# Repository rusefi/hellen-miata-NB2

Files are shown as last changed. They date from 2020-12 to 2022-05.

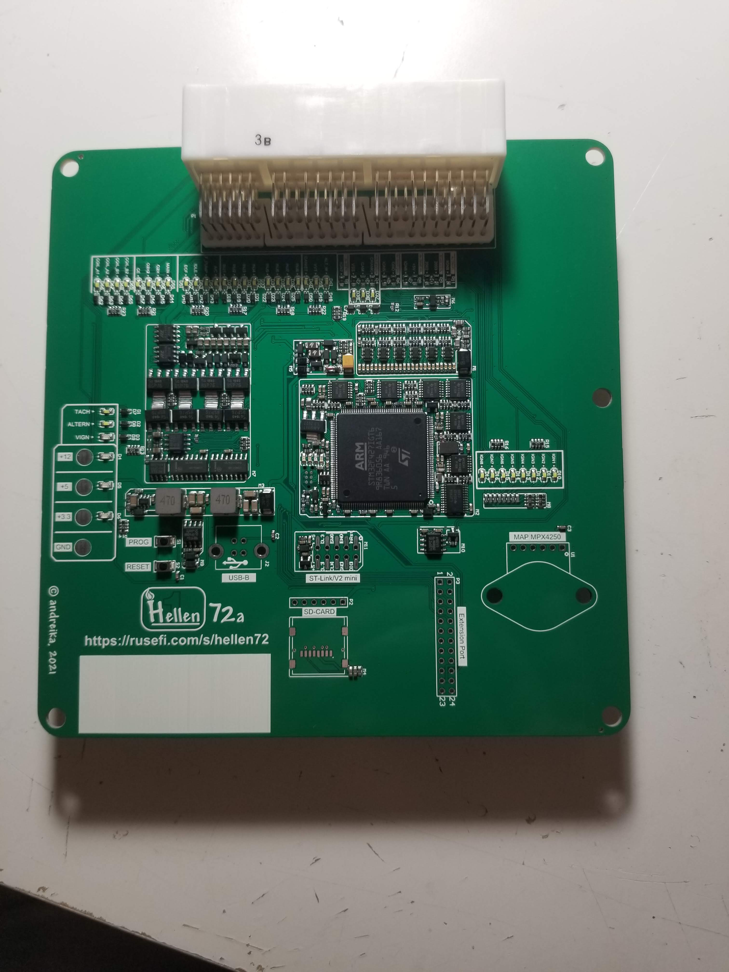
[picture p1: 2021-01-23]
hellen72a.jpg

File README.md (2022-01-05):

# Miata NB2

a rusEFI board with a 72 pin connector. Works for a Mazda Miata NB2 or any generic 8 cylinder vehicle :)

[User Documentation](https://github.com/rusefi/rusefi/wiki/Hellen-NB2)

[Issue Tracker](https://github.com/rusefi/hellen-NB2-issues)

We love https://github.com/thesourcerer8/altium2kicad

https://github.com/rusefi/rusefi/wiki/Mazda-Miata-2001

https://github.com/rusefi/rusefi/wiki/Mazda-Miata-2003

For photos see https://github.com/rusefi/rusefi/wiki/Hellen-NB2

# Compatible cases

89661-3T270

# Hardware

M4 x 10mm will be good for NB external case and internal board to case for both NA and NB.

Powered by https://github.com/andreika-git/hellen-one

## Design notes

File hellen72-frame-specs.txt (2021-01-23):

*** Hellen One: Hellen72 Frame specs (DRAFT) ***

General info: https://rusefi.com/s/hellen72/

EDA Software: Altium Designer

Board/connector footprints source: <.../hw_72_nb>

Pinout spreadsheet: <...>

Modules:
  - mcu/0.1
  - input/0.1
  - output/0.1
  - power5/0.1
  - power12/0.1
  - can/0.1
  - lin/0.1
  - ign8/0.1
  - sd/0.1
  - stlink/0.1
  - knock/0.1

- Additional components:
  - USB-B vertical TH: TE 5787834-1
  - "PROG" button
  - "RESET" button
  - Accelerometer
  - MAP sensor: MPX4250AP
  - SD-Card module connector: <SD-CARD module info>
  - "Extension port" connector: 
    - UART
    - SPI
    - IO1-IO4
    - +3.3V, +5V, +12V, GND

- Board configuration:
  - Jumper resistors for pins:
    - 3L = IN_AFR or OUT_IGN7
    - 3Z = GNDA or OUT_IGN5
    - 4K = V5A or OUT_IGN6
    - 4U = IN_MAP2 or OUT_IGN8
    - IN_VIGN = 4S or 4T
  - Standard input pullups (V5A): 
    - RES1, RES2
    - AUX1, AUX2, AUX3, AUX4
    - TPS, PPS, O2S, O2S2, IAT, CLT
    - CRANK, CAM, VSS
    - SENS3 (FUEL_LEVEL)
  - Standard input pulldowns (GNDA): 
    - MAP1, MAP2, MAP3, MAP4
    - KNOCK
    - SENS1, SENS2, SENS4
  - Additional pulldowns (GNDA):
    - IN_MAF (1k)

- Additional LEDS:
  - IGN1-IGN8 (to GND)
  - INJ1-INJ8 (to +12V, protected)
  - AC, PUMP, IDLE, ECF, VVT, O2H, O2H2, CE, ALT_WARN, MAIN, CANIST (to +12V, protected)
  - TACH, ALTERN, VIGN (to GND, protected)
  - CRANK, CAM, VSS (to +5V, protected)
  - +5V, +3.3V
  - Jumper resistors for LEDS: VSS, CAM, CRANK

- Additional TEST PADS:
  - +12V
  - +5V
  - +3.3V
  - GND

- Silkscreen:
  - silkscreen/board orientation - the ECU connector is at the top
  - all pins named (both sides)
  - https://rusefi.com/s/hellen72/
  - "for notes" area 50x20 mm

- Special layout requirements:
  - SD-Card should be 10-20 mm away from other components
  - MPX4250 hose output opposite to the ECU connector

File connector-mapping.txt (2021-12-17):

(1-30)  1C 1F    1L 1O 1R 1U 1X    2C 2F 2I    2O 2R    3C 3F 3I 3L 3O    3T 3W 3Z    4C 4F 4I 4K 4N    4T 4W    4AB 4AE 4AH
         1  2     3  4  5  6  7     8  9 10    11 12    13 14 15 16 17    18 19 20    21 22 23 24 25    26 27     28  29  30

(31-65) 1B 1E 1H 1K 1N 1Q 1T 1W    2B 2E 2H 2K 2N 2Q    3B 3E 3H 3K 3N 3Q 3S 3V 3Y    4B 4E 4H 4J 4M 4P 4S 4V 4X 4AA 4AD 4AG 
        31 32 33 34 35 36 37 38    39 40 41 42 43 44    45 46 47 48 49 50 51 52 53    54 55 56 57 58 59 60 61 62  63  64  65

(66-94) 1A 1D 1G 1J 1M    1S 1V    2A 2D 2G 2J 2M 2P    3A 3D    3J 3M 3P    3U 3X    4A 4D       4L 4O 4R 4U     4Z 4AC 4AF
        66 67 68 69 70    71 72    73 74 75 76 77 78    79 80    81 82 83    84 85    86 87       88 89 90 91     92  93  94

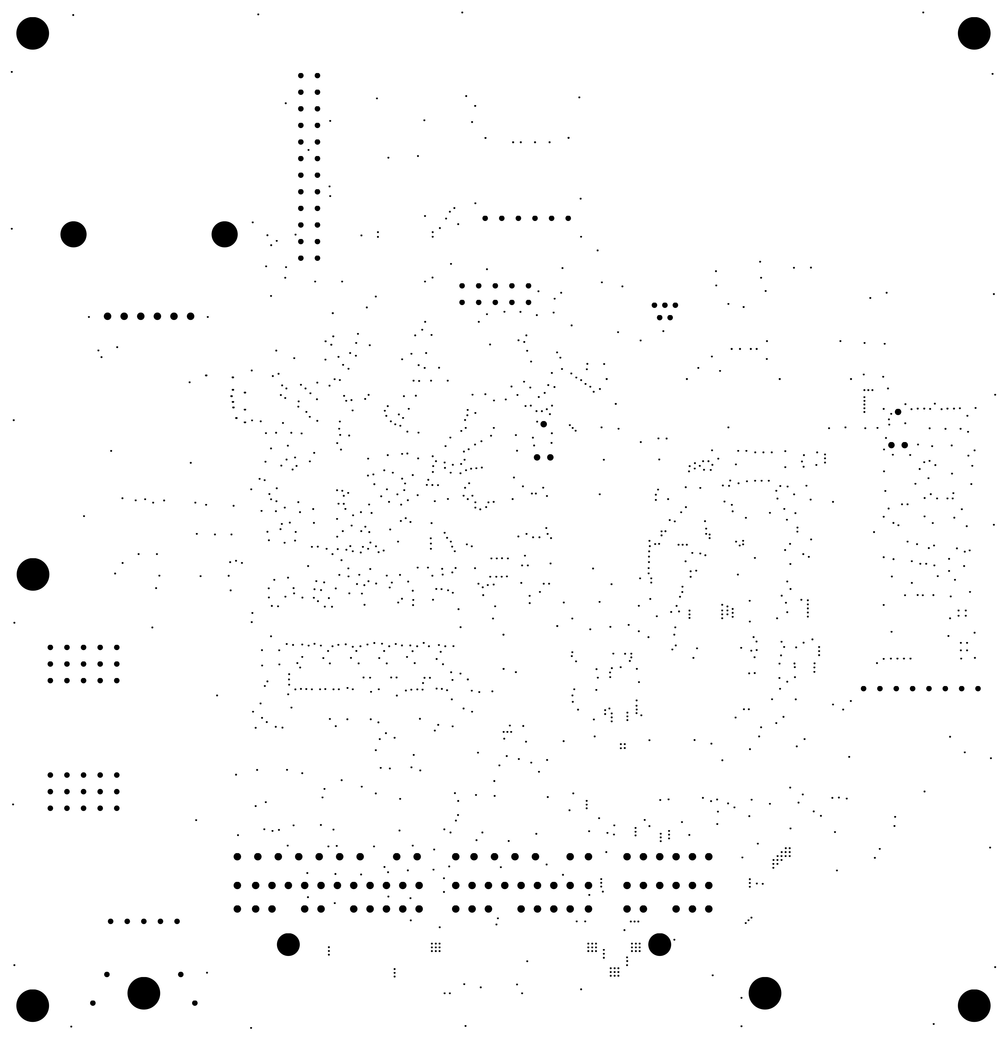
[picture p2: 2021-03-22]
boards/hellen72-c/board/misc/hellen72-c-outline.png

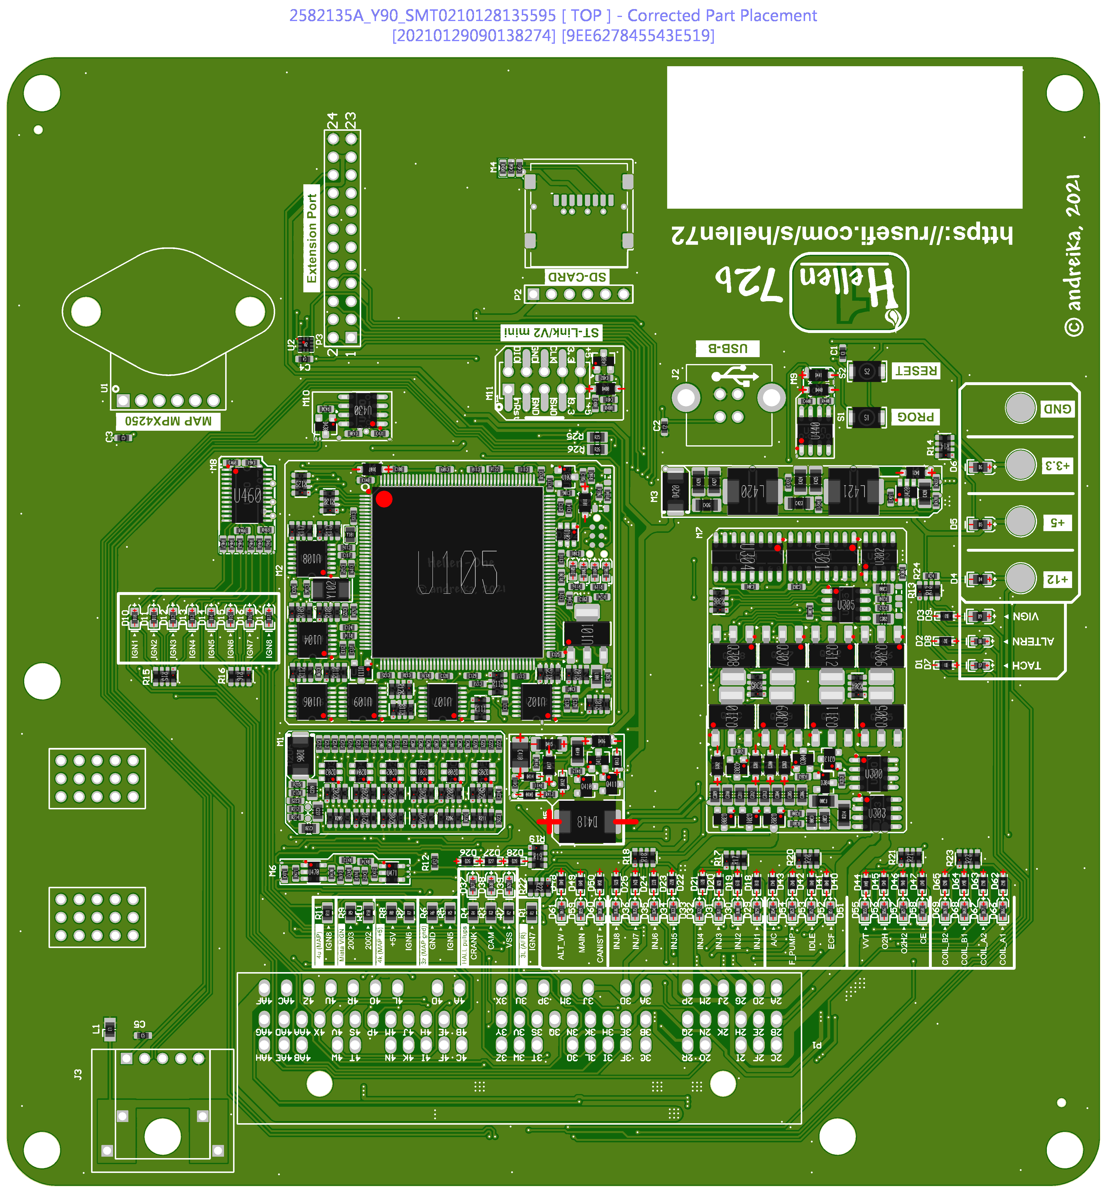
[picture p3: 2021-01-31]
boards/hellen72b/board/Produce_DanZhi.SMT_Snapshot.Top.2582135A_Y90.SMT0210128135595.png

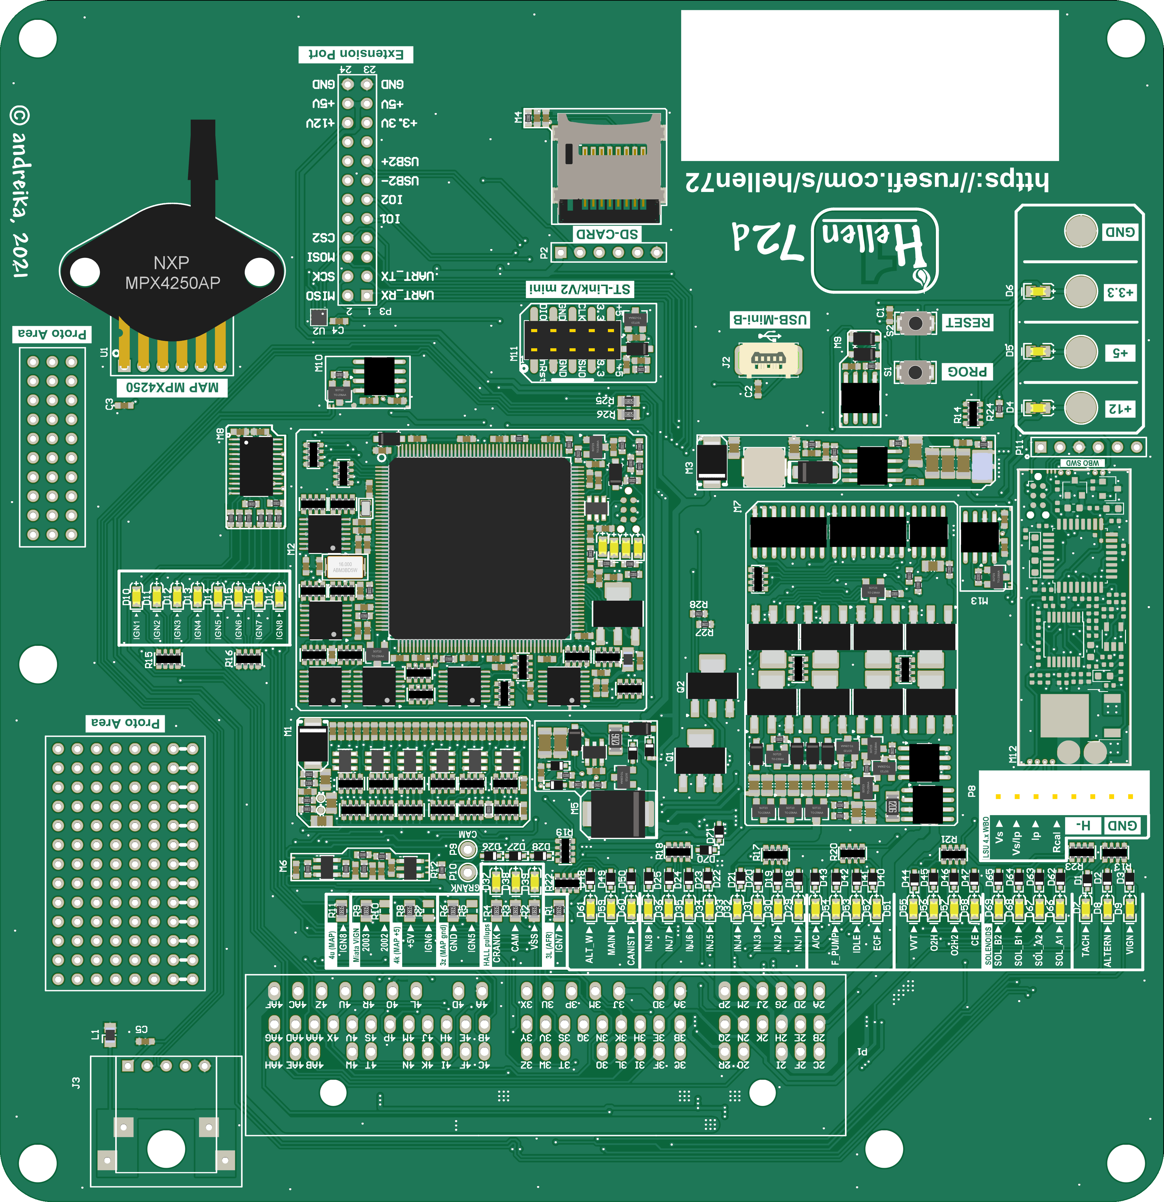
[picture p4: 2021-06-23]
boards/hellen72-d/board/hellen72-d.png

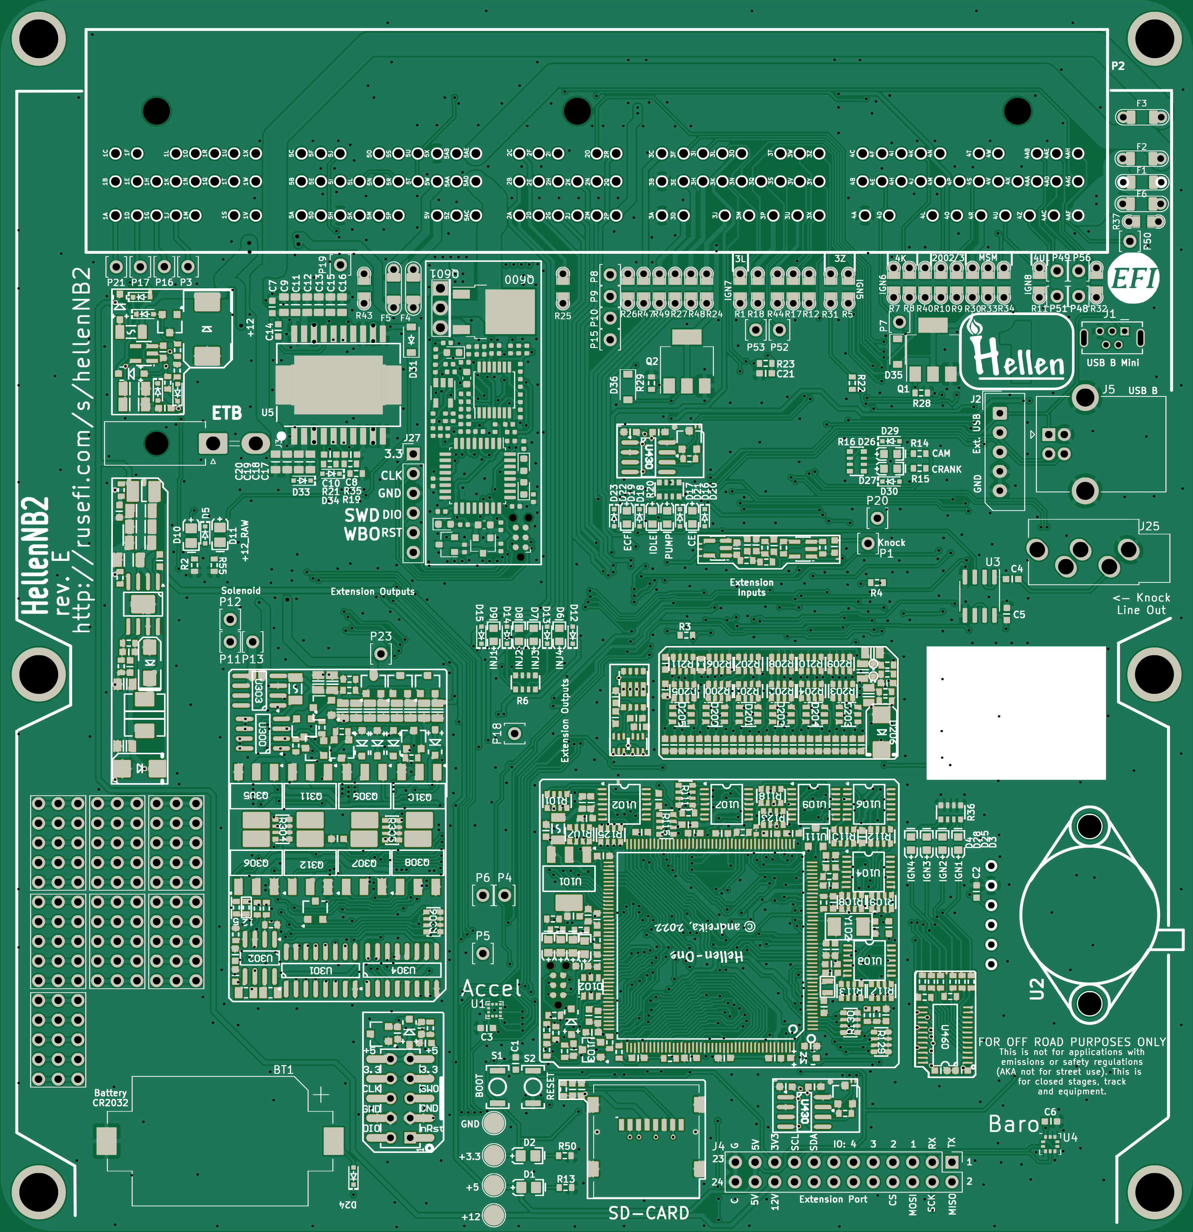
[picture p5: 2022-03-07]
boards/hellen72_NB2-e/board/misc/hellen72_NB2-e-top.png

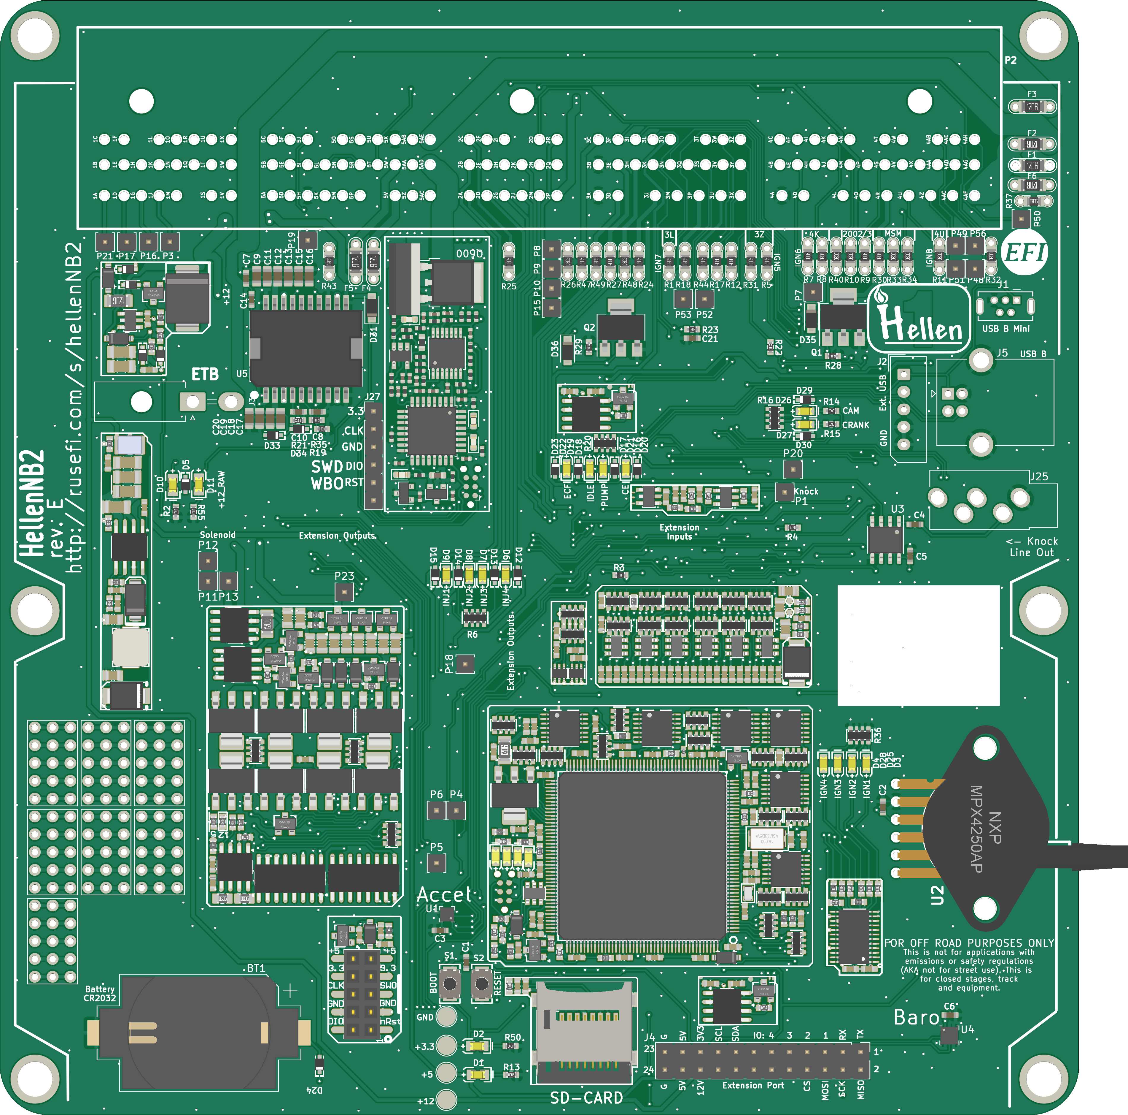
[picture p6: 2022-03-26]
boards/hellen72_NB2-e/board/hellen72_NB2-e.png

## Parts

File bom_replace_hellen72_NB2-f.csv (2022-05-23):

# remove the jumper connection from VCC_PP1 to +5V: we need +12v power supply for push-pull outputs.
R309
# remove +5V pull-ups from SPI1 | because we use it with +3.3v accelerometer
R103
R105
# remove jumper resistor connecting BOOT1 with A22 input line | because we use STM32F4
R131
# STM32
U105 | STM32F407IGT6 | LQFP176 | C33993
# DC-DC Inductor
L421 | MWSA0503S-100MT | SMD-5.2x5.4x2.8 | C408412
L420 | LBC3225T2R2MR | 1210 | C223413
# LMR14020->LMR14030 (more power | no problem)
U420 | LMR14030 | SOP8 | C182078
#fuses
F410 | nSMD050-24V | F1206 | C70076
F300 | nSMD050-24V | F1206 | C70076
F1 | Fuse-5A-1206 | F1206 | C553924
F2 | Fuse-5A-1206 | F1206 | C553924
F3 | Fuse-5A-1206 | F1206 | C553924
F4 | Fuse-5A-1206 | F1206 | C553924
F5 | Fuse-5A-1206 | F1206 | C553924
F6 | Fuse-5A-1206 | F1206 | C553924
#INJ low-side
Q305 | ZXMS6005SGTA | SOT-223 | C174042
Q306 | ZXMS6005SGTA | SOT-223 | C174042
Q307 | ZXMS6005SGTA | SOT-223 | C174042
Q308 | ZXMS6005SGTA | SOT-223 | C174042
Q309 | ZXMS6005SGTA | SOT-223 | C174042
Q310 | ZXMS6005SGTA | SOT-223 | C174042
Q311 | ZXMS6005SGTA | SOT-223 | C174042
Q312 | ZXMS6005SGTA | SOT-223 | C174042
#power distribution
U103 | AP2331W-7 | SOT-23 | C460346
U480 | AP2331W-7 | SOT-23 | C460346
##### 2022-03-08 JLC stock replacements:
#green LED 0805
D1 | LED-GREEN-0805 | C434432
D2 | LED-GREEN-0805 | C434432
D10 | LED-GREEN-0805 | C434432
D11 | LED-GREEN-0805 | C434432
#wbo opamp
U601 | GS8551-TR | TSOT23-5 | C157715
#wbo low-side
Q600 | VND14NV04TR-E | DPAK | C2649436
Q600_2 | VND14NV04TR-E | DPAK | C2649436
#capacitor 10uF 25V 0603
C300 | 10u | C0603 | C2922482
# ignition buffer
U460 | 74LVC4245APW | TSSOP24 | C6091
# trigger schmidt buffer
U490 | SN74LVC2G17DCKR | SOT-363 | C50714
U491 | SN74LVC2G17DCKR | SOT-363 | C50714
#p-channel mosfets
Q300 | WST4045 | SOT-23 | C719073
Q301 | WST4045 | SOT-23 | C719073
Q302 | WST4045 | SOT-23 | C719073
Q303 | WST4045 | SOT-23 | C719073
Q304 | WST4045 | SOT-23 | C719073
Q313 | WST4045 | SOT-23 | C719073
Q314 | WST4045 | SOT-23 | C719073
#pressure sensor
U4 | LPS22HBTR | HLGA-10 | C94049
#non-JLC componentts
#WBO low-side
Q601
Q601_2
#WBO STM32
U602
U602_2
#include board_id_72_NB2-f.csv

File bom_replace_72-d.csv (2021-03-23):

# remove the jumper connection from VCC_PP1 to +5V: we need +12v power supply for push-pull outputs.
R309
# remove +5V pull-ups from SPI1 | because we use it with +3.3v accelerometer
R103
R105
# remove jumper resistor connecting BOOT1 with A22 input line | because we use STM32F4
R131
# JLC stock adjustments
U103 | AP2331TDSA-7 | SOT-23 | C183303
U480 | AP2331TDSA-7 | SOT-23 | C183303
U600 | LMV324IPWR | TSSOP14 | C398929

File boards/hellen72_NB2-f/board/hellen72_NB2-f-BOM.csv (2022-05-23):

Comment | Designator | Footprint | LCSC Part #
BATTERY_CR2032 | BT1 | BATTERY-2032 | C70377
100n | C1, C2, C3, C5, C6, C7, C204, C205, C206, C207, C212, C213, C214, C215, C220, C221, C222, C223, C224, C225, C226, C460, C461, C101, C105, C106, C107, C108, C109, C110, C111, C112, C113, C117, C118, C119, C120, C121, C122, C123, C124, C125, C126, C127, C128, C129, C130, C135, C139, C480, C481, C482, C430, C431, C470, C411, C413, C420, C430_2, C431_2 | C0603 | C14663
10u | C4 | C0603 | C19702
6.8n | C8 | C0603 | C1631
10u | C9, C11, C12, C13, C15, C16, C17, C18, C19, C20, C304, C305, C306, C307, C308, C309, C310, C311, C312, C313, C425, C426 | C0805 | C15850
10n | C10, C201, C208, C209, C210, C211, C301, C302, C428 | C0603 | C57112
220n | C14 | C0603 | C21120
100n | C21 | C0603
LED-BLUE-0603 | D3, D4, D25, D28, D105, D602 | LED-0603 | C72041
1N4148WS | D5, D12, D13, D14, D15, D20, D21, D22, D23, D24, D29, D30, D33, D34, D410, D412, D413, D414 | SOD-323 | C2128
LED-RED-0603 | D6, D7, D8, D9, D103, D600, D603 | LED-0603 | C2286
LED-WHITE-0603 | D16, D17, D18, D19, D26, D27 | LED-0603 | C2290
B5819W | D31, D35, D36, D101, D107, D300, D301, D302, D303, D480, D416, D417 | SOD-123 | C8598
LOGO | G1 | LOGO
DISCLAIMER | G2 | Off_Road_Disclaimer
LOGO | G3 | LOGO
PROTO_AREA | G4 | PROTO_AREA
PROTO_AREA | G5 | PROTO_AREA
PROTO_AREA | G6 | PROTO_AREA
PROTO_AREA | G7 | PROTO_AREA
PROTO_AREA | G9 | PROTO_AREA
PROTO_AREA | G11 | PROTO_AREA
PROTO_AREA | G12 | PROTO_AREA
USB_B_Mini | J1 | USB-MINI-B-VERTICAL | C13453
Conn_01x05_Male | J2 | Molex_SPOX_5267-05A_1x05_P2.50mm_Vertical
MiniFit | J3 | Molex-39301020 | C240832
Conn_02x12_Odd_Even | J4 | PinHeader_2x12_P2.54mm_Vertical
USB_B | J5 | USB_B | C46392
Conn_01x01 | J11 | MountingHole_4.5mm_Pad
Conn_01x01 | J13 | MountingHole_4.5mm_Pad
Conn_01x01 | J14 | MountingHole_4.5mm_Pad
Conn_01x01 | J15 | MountingHole_4.5mm_Pad
Conn_01x01 | J16 | MountingHole_4.5mm_Pad
Conn_01x01 | J17 | MountingHole_4.5mm_Pad
Conn_01x01 | J19 | TestPoint_Pad_D2.0mm
Conn_01x01 | J20 | TestPoint_Pad_D2.0mm
Conn_01x01 | J21 | TestPoint_Pad_D2.0mm
Conn_01x01 | J22 | TestPoint_Pad_D2.0mm
Conn_01x01 | J24 | TestPoint_Pad_D2.0mm
AudioJack3_SwitchTR | J25 | Jack_3.5mm_PJ-3250-5A | C165947
Conn_01x06 | J27 | PinHeader_1x06_P2.54mm_Vertical
Pad | P1 | PAD-TH
8-5353015-1 | P2 | 8-5353015-1
Pad | P3 | PAD-TH
Pad | P4 | PAD-TH
Pad | P5 | PAD-TH
Pad | P6 | PAD-TH
Pad | P7 | PAD-TH
Pad | P8 | PAD-TH
Pad | P9 | PAD-TH
Pad | P10 | PAD-TH
Pad | P11 | PAD-TH
Pad | P12 | PAD-TH
Pad | P13 | PAD-TH
Pad | P15 | PAD-TH
Pad | P16 | PAD-TH
Pad | P17 | PAD-TH
Pad | P18 | PAD-TH
Pad | P19 | PAD-TH
Pad | P20 | PAD-TH
Pad | P21 | PAD-TH
Pad | P23 | PAD-TH
Pad | P48 | PAD-TH
Pad | P49 | PAD-TH
Pad | P50 | PAD-TH
Pad | P51 | PAD-TH
Pad | P52 | PAD-TH
Pad | P53 | PAD-TH
Pad | P56 | PAD-TH
AUIPS2041LTR | Q1, Q2 | SOT-223 | C113610
Jumper-Pad-Pad | R1 | PAD-0805-PAD
5.1k | R2, R55, R132 | R0603 | C23186
4.7k | R3, R302, R303, R313 | R0603 | C23162
1k | R4, R311, R314 | R0603 | C21190
Jumper-Pad-Pad | R5 | PAD-0805-PAD
4.7k | R6, R16, R200, R201, R202, R203, R204, R205, R207 | R0603-4 | C1980
Jumper-Pad-Pad | R7 | PAD-0805-PAD
Jumper-Pad-Pad | R8, R9, R12, R17, R18, R24, R25, R26, R27, R30, R31, R32, R34, R38, R39, R40, R43, R44, R47, R48, R49 | PAD-0805-PAD | C17477
Jumper-Pad-Pad | R10 | PAD-0805-PAD
Jumper-Pad-Pad | R11 | PAD-0805-PAD
1.6k | R13 | R0603 | C22847
0 | R14, R15, R23, R310 | R0603 | C21189
10k | R19, R28, R29, R102, R121, R127, R128, R300, R301, R307, R308, R315, R480, R421, R134 | R0603 | C25804
20k | R20 | R0603-4 | C12004
100 | R21, R104, R106 | R0603 | C22775
680k | R22 | R0603 | C25822
Jumper-Pad-Pad | R33 | PAD-0805-PAD
100k | R35, R471, R473 | R0603 | C25803
470 | R36 | R0603-4 | C25510
Jumper-Pad-Pad | R37 | PAD-0805-PAD
750 | R50 | R0603 | C23241
Button_SPST | S1, S2 | SMD-2_2.9x3.9x1.7 | C115357
LIS2DW12TR | U1 | LGA-12_2x2mm_P0.5mm | C189624
MPX4_MAP | U2 | MPX-4_MAP
MCP6002-xSN | U3 | SO8 | C7377
L6205PD | U5 | SO20POWER | C36543
1n | C200, C202, C203, C216, C217, C218, C219, C490, C491, C492, C493 | C0603 | C1588
2.2u | C227, C228, C229 | C0805 | C49217
SRV05-4-P-T7 | D200, D201, D202, D203, D204, D205, D102 | SOT23-6 | C85364
P6SMB6.8CA | D206, D421 | SMB | C78395
680k | R206, R209, R211, R490 | R0603-4 | C145776
10k | R208, R210, R129, R130, R304, R305, R306, R491 | R0603-4 | C29718
510 | R212, R213, R214, R215, R116, R119, R120, R124, R133 | R0603 | C23193
3.3k | R216 | R0603 | C22978
10 | R461, R462, R463, R464, R466, R467, R468, R469 | R0603 | C22859
4.7u | C102, C103, C104, C137, C138, C140, C427, C616 | C0603 | C19666
2.2u | C114, C131 | C0603 | C23630
12p | C115, C116 | C0603 | C38523
18p | C132, C136 | C0603 | C1647
1u | C133 | C0603 | C15849
LED-GREEN-0603 | D104, D601 | LED-0603 | C72043
LED-YELLOW-0603 | D106 | LED-0603 | C72038
SMD1206B035TF/16 | F101 | SMD1206 | C269114
4.7k | R101, R107, R108, R109, R110, R111, R112, R113, R115, R117, R118, R125, R126 | R0603-4 | C66697
47 | R114 | R0603 | C23182
2.2k | R122, R123 | R0603 | C4190
AMS1117-3.3 | U101 | SOT-223 | C6186
MCP6004 | U102, U104, U106, U107, U108, U109, U600 | TSSOP14 | C50282
XC6206P332MR | U111, U604 | SOT-23 | C5446
32.768 kHz | Y101 | SMD2012 | C99009
20 MHz | Y102 | SMD5032 | C112566
22u | C450, C451 | C0603 | C59461
Molex MicroSD 47219-2001 | J450 | SDAMB-012 | C164170
33k | R450, R474, R411 | R0603 | C4216
PSM712-LF | D304, D305, D411 | SOT-23 | C32677
100 | R312, R316 | R0805 | C17408
RZ7899 | U300, U303 | SO8 | C92373
ULN2003AD | U301, U304 | SOIC16 | C7512
TC4427 | U302 | SO8 | C20551
ST/Link 2x5 | P480 | HDR2x5-F-TH-SMD
PESD1CAN | D430, D430_2 | SOT-23 | C343993
120 | R430, R430_2 | R0603 | C22787
TJA1051T/3/1J | U430, U430_2 | SO8 | C38695
3.3n | C471 | C0603 | C1613
330p | C472 | C0603 | C1664
47p | C473 | C0603 | C1671
680p | C474 | C0603 | C1630
470k | R470 | R0603 | C23178
12k | R472, R423 | R0603 | C22790
LMV321IDBVR | U470, U471 | SOT23-5 | C7972
47u | C410, C412 | C1206 | C96123
SMCJ30A | D418 | SMC | C310046
6.8k | R410, R413 | R0603 | C23212
MIC5205-3.3YM5 | U410 | SOT23-5 | C37970
10u | C421, C422, C423, C424 | C1206 | C13585
220p | C429 | C0603 | C1603
SS34 | D420 | SMA | C8678
1 | R420 | R0603 | C22936
68k | R422 | R0603 | C23231
1u | C600, C607, C609, C610, C611 | C0402 | C52923
100n | C601, C602, C605, C608, C612, C613, C614, C615 | C0402 | C1525
33n | C603 | C0402 | C1585
DNP | C604 | C0402
DNP | C606 | C0402
1k | R600, R601, R616, R617, R622, R626, R627, R628 | R0402 | C11702
68k | R602, R603 | R0402 | C36871
10k | R604, R605, R613, R614, R618, R619, R625 | R0402 | C25744
10 | R606 | R0402 | C25077
22k | R607 | R0402 | C25768
47 | R608 | R0402 | C25118
61.9 | R609 | R0603 | C23092
20k | R610, R611, R612 | R0402 | C25765
100k | R615, R621 | R0402 | C25741
27k | R620, R623 | R0402 | C25771
3.3k | R624 | R0402 | C25890
REF3033 | U603 | SOT-23 | C36658
STM32F407IGT6 | U105 | LQFP176 | C33993
MWSA0503S-100MT | L421 | SMD-5.2x5.4x2.8 | C408412
LBC3225T2R2MR | L420 | 1210 | C223413
LMR14030 | U420 | SOP8 | C182078
nSMD050-24V | F410, F300 | F1206 | C70076
Fuse-5A-1206 | F1, F2, F3, F4, F5, F6 | F1206 | C553924
ZXMS6005SGTA | Q305, Q306, Q307, Q308, Q309, Q310, Q311, Q312 | SOT-223 | C174042
AP2331W-7 | U103, U480 | SOT-23 | C460346
GS8551-TR | U601 | TSOT23-5 | C157715
VND14NV04TR-E | Q600, Q600_2 | DPAK | C2649436
10u | C300 | C0603 | C2922482
74LVC4245APW | U460 | TSSOP24 | C6091
SN74LVC2G17DCKR | U490, U491 | SOT-363 | C50714
WST4045 | Q300, Q301, Q302, Q303, Q304, Q313, Q314 | SOT-23 | C719073
LPS22HBTR | U4 | HLGA-10 | C94049

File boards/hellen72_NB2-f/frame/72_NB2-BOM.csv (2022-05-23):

Comment | Designator | Footprint | LCSC Part #
BATTERY_CR2032 | BT1 | BATTERY-2032 | C70377
100n | C1 | C0603 | C14663
100n | C2 | C0603 | C14663
100n | C3 | C0603 | C14663
10u | C4 | C0603 | C19702
100n | C5 | C0603 | C14663
100n | C6 | C0603 | C14663
100n | C7 | C0603 | C14663
6.8n | C8 | C0603 | C1631
10u | C9 | C0805 | C15850
10n | C10 | C0603 | C57112
10u | C11 | C0805 | C15850
10u | C12 | C0805 | C15850
10u | C13 | C0805 | C15850
220n | C14 | C0603 | C21120
10u | C15 | C0805 | C15850
10u | C16 | C0805 | C15850
10u | C17 | C0805 | C15850
10u | C18 | C0805 | C15850
10u | C19 | C0805 | C15850
10u | C20 | C0805 | C15850
100n | C21 | C0603
LED-GREEN-0805 | D1 | LED-0805 | C2297
LED-GREEN-0805 | D2 | LED-0805 | C2297
LED-BLUE-0603 | D3 | LED-0603 | C72041
LED-BLUE-0603 | D4 | LED-0603 | C72041
1N4148WS | D5 | SOD-323 | C2128
LED-RED-0603 | D6 | LED-0603 | C2286
LED-RED-0603 | D7 | LED-0603 | C2286
LED-RED-0603 | D8 | LED-0603 | C2286
LED-RED-0603 | D9 | LED-0603 | C2286
LED-GREEN-0805 | D10 | LED-0805 | C2297
LED-GREEN-0805 | D11 | LED-0805 | C2297
1N4148WS | D12 | SOD-323 | C2128
1N4148WS | D13 | SOD-323 | C2128
1N4148WS | D14 | SOD-323 | C2128
1N4148WS | D15 | SOD-323 | C2128
LED-WHITE-0603 | D16 | LED-0603 | C2290
LED-WHITE-0603 | D17 | LED-0603 | C2290
LED-WHITE-0603 | D18 | LED-0603 | C2290
LED-WHITE-0603 | D19 | LED-0603 | C2290
1N4148WS | D20 | SOD-323 | C2128
1N4148WS | D21 | SOD-323 | C2128
1N4148WS | D22 | SOD-323 | C2128
1N4148WS | D23 | SOD-323 | C2128
1N4148WS | D24 | SOD-323 | C2128
LED-BLUE-0603 | D25 | LED-0603 | C72041
LED-WHITE-0603 | D26 | LED-0603 | C2290
LED-WHITE-0603 | D27 | LED-0603 | C2290
LED-BLUE-0603 | D28 | LED-0603 | C72041
1N4148WS | D29 | SOD-323 | C2128
1N4148WS | D30 | SOD-323 | C2128
B5819W | D31 | SOD-123 | C8598
1N4148WS | D33 | SOD-323 | C2128
1N4148WS | D34 | SOD-323 | C2128
B5819W | D35 | SOD-123 | C8598
B5819W | D36 | SOD-123 | C8598
Fuse-Pad-Pad | F1 | PAD-1206-PAD | C182446
Fuse-Pad-Pad | F2 | PAD-1206-PAD | C182446
Fuse-Pad-Pad | F3 | PAD-1206-PAD | C182446
Fuse-Pad-Pad | F4 | PAD-1206-PAD | C182446
Fuse-Pad-Pad | F5 | PAD-1206-PAD | C182446
Fuse-Pad-Pad | F6 | PAD-1206-PAD | C182446
LOGO | G1 | LOGO
DISCLAIMER | G2 | Off_Road_Disclaimer
LOGO | G3 | LOGO
PROTO_AREA | G4 | PROTO_AREA
PROTO_AREA | G5 | PROTO_AREA
PROTO_AREA | G6 | PROTO_AREA
PROTO_AREA | G7 | PROTO_AREA
PROTO_AREA | G9 | PROTO_AREA
PROTO_AREA | G11 | PROTO_AREA
PROTO_AREA | G12 | PROTO_AREA
USB_B_Mini | J1 | USB-MINI-B-VERTICAL | C13453
Conn_01x05_Male | J2 | Molex_SPOX_5267-05A_1x05_P2.50mm_Vertical
MiniFit | J3 | Molex-39301020 | C240832
Conn_02x12_Odd_Even | J4 | PinHeader_2x12_P2.54mm_Vertical
USB_B | J5 | USB_B | C46392
Conn_01x01 | J11 | MountingHole_4.5mm_Pad
Conn_01x01 | J13 | MountingHole_4.5mm_Pad
Conn_01x01 | J14 | MountingHole_4.5mm_Pad
Conn_01x01 | J15 | MountingHole_4.5mm_Pad
Conn_01x01 | J16 | MountingHole_4.5mm_Pad
Conn_01x01 | J17 | MountingHole_4.5mm_Pad
Conn_01x01 | J19 | TestPoint_Pad_D2.0mm
Conn_01x01 | J20 | TestPoint_Pad_D2.0mm
Conn_01x01 | J21 | TestPoint_Pad_D2.0mm
Conn_01x01 | J22 | TestPoint_Pad_D2.0mm
Conn_01x01 | J24 | TestPoint_Pad_D2.0mm
AudioJack3_SwitchTR | J25 | Jack_3.5mm_PJ-3250-5A | C165947
Conn_01x06 | J27 | PinHeader_1x06_P2.54mm_Vertical
Module:input/0.1 | M1 | input
Module:ign8/0.2 | M2 | ign8
Module:mcu/0.6 | M3 | mcu
Module:sd/0.1 | M4 | sd
Module:output/0.3 | M5 | output
Module:dinput4/0.1 | M6 | dinput4
Module:stlink/0.1 | M7 | stlink
Module:can/0.1 | M8 | can
Module:knock/0.1 | M9 | knock
Module:power12/0.2 | M10 | power12
Module:power5/0.2 | M11 | power5
Module:wbo/0.3 | M12 | wbo
Module:can/0.1 | M13 | can
Pad | P1 | PAD-TH
8-5353015-1 | P2 | 8-5353015-1
Pad | P3 | PAD-TH
Pad | P4 | PAD-TH
Pad | P5 | PAD-TH
Pad | P6 | PAD-TH
Pad | P7 | PAD-TH
Pad | P8 | PAD-TH
Pad | P9 | PAD-TH
Pad | P10 | PAD-TH
Pad | P11 | PAD-TH
Pad | P12 | PAD-TH
Pad | P13 | PAD-TH
Pad | P15 | PAD-TH
Pad | P16 | PAD-TH
Pad | P17 | PAD-TH
Pad | P18 | PAD-TH
Pad | P19 | PAD-TH
Pad | P20 | PAD-TH
Pad | P21 | PAD-TH
Pad | P23 | PAD-TH
Pad | P48 | PAD-TH
Pad | P49 | PAD-TH
Pad | P50 | PAD-TH
Pad | P51 | PAD-TH
Pad | P52 | PAD-TH
Pad | P53 | PAD-TH
Pad | P56 | PAD-TH
AUIPS2041LTR | Q1 | SOT-223 | C113610
AUIPS2041LTR | Q2 | SOT-223 | C113610
Jumper-Pad-Pad | R1 | PAD-0805-PAD
5.1k | R2 | R0603 | C23186
4.7k | R3 | R0603 | C23162
1k | R4 | R0603 | C21190
Jumper-Pad-Pad | R5 | PAD-0805-PAD
4.7k | R6 | R0603-4 | C1980
Jumper-Pad-Pad | R7 | PAD-0805-PAD
Jumper-Pad-Pad | R8 | PAD-0805-PAD | C17477
Jumper-Pad-Pad | R9 | PAD-0805-PAD | C17477
Jumper-Pad-Pad | R10 | PAD-0805-PAD
Jumper-Pad-Pad | R11 | PAD-0805-PAD
Jumper-Pad-Pad | R12 | PAD-0805-PAD | C17477
1.6k | R13 | R0603 | C22847
0 | R14 | R0603 | C21189
0 | R15 | R0603 | C21189
4.7k | R16 | R0603-4 | C1980
Jumper-Pad-Pad | R17 | PAD-0805-PAD | C17477
Jumper-Pad-Pad | R18 | PAD-0805-PAD | C17477
10k | R19 | R0603 | C25804
20k | R20 | R0603-4 | C12004
100 | R21 | R0603 | C22775
680k | R22 | R0603 | C25822
0 | R23 | R0603 | C21189
Jumper-Pad-Pad | R24 | PAD-0805-PAD | C17477
Jumper-Pad-Pad | R25 | PAD-0805-PAD | C17477
Jumper-Pad-Pad | R26 | PAD-0805-PAD | C17477
Jumper-Pad-Pad | R27 | PAD-0805-PAD | C17477
10k | R28 | R0603 | C25804
10k | R29 | R0603 | C25804
Jumper-Pad-Pad | R30 | PAD-0805-PAD | C17477
Jumper-Pad-Pad | R31 | PAD-0805-PAD | C17477
Jumper-Pad-Pad | R32 | PAD-0805-PAD | C17477
Jumper-Pad-Pad | R33 | PAD-0805-PAD
Jumper-Pad-Pad | R34 | PAD-0805-PAD | C17477
100k | R35 | R0603 | C25803
470 | R36 | R0603-4 | C25510
Jumper-Pad-Pad | R37 | PAD-0805-PAD
Jumper-Pad-Pad | R38 | PAD-0805-PAD | C17477
Jumper-Pad-Pad | R39 | PAD-0805-PAD | C17477
Jumper-Pad-Pad | R40 | PAD-0805-PAD | C17477
Jumper-Pad-Pad | R43 | PAD-0805-PAD | C17477
Jumper-Pad-Pad | R44 | PAD-0805-PAD | C17477
Jumper-Pad-Pad | R47 | PAD-0805-PAD | C17477
Jumper-Pad-Pad | R48 | PAD-0805-PAD | C17477
Jumper-Pad-Pad | R49 | PAD-0805-PAD | C17477
750 | R50 | R0603 | C23241
5.1k | R55 | R0603 | C23186
Button_SPST | S1 | SMD-2_2.9x3.9x1.7 | C115357
Button_SPST | S2 | SMD-2_2.9x3.9x1.7 | C115357
LIS2DW12TR | U1 | LGA-12_2x2mm_P0.5mm | C189624
MPX4_MAP | U2 | MPX-4_MAP
MCP6002-xSN | U3 | SO8 | C7377
LPS25HB | U4 | HLGA-10 | C87898
L6205PD | U5 | SO20POWER | C36543

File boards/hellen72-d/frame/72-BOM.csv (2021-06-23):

Comment | Designator | Footprint | LCSC Part #
100n | C1, C2, C3, C4, C5 | C0603 | C14663
1N4148WS | D1, D2, D3, D18, D19, D20, D21, D22, D23, D24, D25, D26, D27, D28, D40, D41, D42, D43, D44, D45, D46, D47, D48, D49, D50, D62, D63, D64, D65, D70, D71 | SOD-323 | C2128
LED-GREEN-0805 | D4, D5, D6 | LED-0805 | C2297
LED-WHITE-0603 | D7, D8, D51, D52, D53, D54, D55, D56, D57, D58, D59, D60, D61, D66, D67, D68, D69 | LED-0603 | C2290
LED-GREEN-0603 | D9 | LED-0603 | C72043
LED-BLUE-0603 | D10, D11, D12, D13, D14, D15, D16, D17 | LED-0603 | C72041
LED-RED-0603 | D29, D30, D31, D32, D33, D34, D35, D36, D37, D38, D39 | LED-0603 | C2286
USB-Mini-V | J2 | USB-B-VERTICAL | C13453
USB-Adapter | J3 | USB-B-VERTICAL
GZ2012D101TF | L1 | L0805 | C1015
Module:input/0.1 | M1
Module:mcu/0.3 | M2
Module:power5/0.2 | M3
Module:sd/0.1 | M4
Module:power12/0.2 | M5
Module:knock/0.1 | M6
Module:output/0.2 | M7
Module:ign8/0.1 | M8
Module:lin/0.1 | M9
Module:can/0.1 | M10, M13
Module:stlink/0.1 | M11
Module:wbo/0.2 | M12
XH-8A | P8 | CONN-XH-8A | C146110
CAM | P9
CRANK | P10
WBO SWD | P11
AUIPS2041LTR | Q1, Q2 | SOT-223 | C113610
0 | R1, R2, R3, R4, R6, R8, R9, R11, R25, R26 | R0805 | C17477
1k | R12 | R0603 | C21190
10k | R13, R20, R21, R22, R23 | R0603-4 | C29718
1k | R14, R19 | R0603-4 | C20197
470 | R15, R16 | R0603-4 | C25510
4.7k | R17, R18 | R0603-4 | C1980
2.2k | R24 | R0603 | C4190
10k | R27, R28 | R0603 | C25804
Switch SPST | S1, S2 | SMD-2_2.9x3.9x1.7 | C115357
Abs. Pressure Sensor | U1 | 867B
LIS2DW12TR | U2 | LGA12 | C189624

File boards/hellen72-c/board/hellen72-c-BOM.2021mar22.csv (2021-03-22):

Comment | Designator | Footprint | LCSC Part #
100n | C1, C2, C3, C4, C5, C204, C205, C206, C207, C212, C213, C214, C215, C220, C221, C222, C223, C224, C225, C226, C101, C105, C106, C107, C108, C109, C110, C111, C112, C113, C117, C118, C119, C120, C121, C122, C123, C124, C125, C126, C127, C128, C129, C130, C135, C139, C420, C411, C470, C460, C461, C440, C430, C431, C480, C481, C482 | C0603 | C14663
1N4148WS | D1, D2, D3, D18, D19, D20, D21, D22, D23, D24, D25, D26, D27, D28, D40, D41, D42, D43, D44, D45, D46, D47, D48, D49, D50, D62, D63, D64, D65, D70, D71, D72, D410, D412, D413, D414 | SOD-323 | C2128
LED-GREEN-0805 | D4, D5, D6 | LED-0805 | C2297
LED-WHITE-0603 | D7, D8, D39, D51, D52, D53, D54, D55, D56, D57, D58, D59, D60, D61, D66, D67, D68, D69 | LED-0603 | C2290
LED-GREEN-0603 | D9, D104, D601 | LED-0603 | C72043
LED-BLUE-0603 | D10, D11, D12, D13, D14, D15, D16, D17, D105, D602 | LED-0603 | C72041
LED-RED-0603 | D29, D30, D31, D32, D33, D34, D35, D36, D37, D38, D103, D600, D603 | LED-0603 | C2286
USB-Mini-V | J2 | USB-B-VERTICAL | C13453
USB-Adapter | J3 | USB-B-VERTICAL
GZ2012D101TF | L1 | L0805 | C1015
XH-8A | P8 | CONN-XH-8A | C146110
AUIPS2041LTR | Q1, Q2, Q305, Q306, Q307, Q308, Q309, Q310, Q311, Q312 | SOT-223 | C113610
0 | R1, R2, R3, R4, R6, R8, R9, R10, R11, R25, R26 | R0805 | C17477
1k | R12, R440 | R0603 | C21190
4k7 | R13, R17, R18, R20, R21, R22, R23, R200, R201, R202, R203, R204, R205, R207 | R0603-4 | C1980
470 | R14, R15, R16, R19 | R0603-4 | C25510
2.2k | R24 | R0603 | C4190
3.3k | R27, R216 | R0603 | C22978
Switch SPST | S1, S2 | SMD-2_2.9x3.9x1.7 | C115357
Abs. Pressure Sensor | U1 | 867B
QMA7981 | U2 | LGA12 | C457290
1n | C200, C202, C203, C216, C217, C218, C219 | C0603 | C1588
10n | C201, C208, C209, C210, C211, C428 | C0603 | C57112
2.2u | C227, C228, C229 | C0805 | C49217
SRV05-4-P-T7 | D200, D201, D202, D203, D204, D205, D102 | SOT23-6 | C85364
P6SMB6.8CA | D206, D421 | SMB | C78395
680k | R206, R209, R211 | R0603-4 | C145776
10k | R208, R210, R129, R130, R304, R305, R306 | R0603-4 | C29718
510 | R212, R213, R214, R215, R116, R119, R120, R124 | R0603 | C23193
4.7u | C102, C103, C104, C137, C138, C140, C427, C616 | C0603 | C19666
2.2u | C114, C131 | C0603 | C23630
12p | C115, C116 | C0603 | C38523
18p | C132, C136 | C0603 | C1647
B5819W | D101, D107, D416, D417, D300, D301, D302, D303, D440, D441, D480 | SOD-123 | C8598
LED-YELLOW-0603 | D106 | LED-0603 | C72038
SDFL2012Q3R3KTF | L101 | L0805 | C51725
4k7 | R101, R107, R108, R109, R110, R111, R112, R113, R115, R117, R118, R125, R126 | R0603-4 | C66697
10k | R102, R121, R122, R123, R127, R128, R421, R300, R301, R480 | R0603 | C25804
100 | R104, R106 | R0603 | C22775
47 | R114 | R0603 | C23182
AMS1117-3.3 | U101 | SOT-223 | C6186
LMV324IPWR | U102, U104, U106, U107, U108, U109 | TSSOP14 | C398929
STM32F427IGT6 | U105 | LQFP176 | C75389
XC6206P332MR | U111, U604 | SOT-23 | C5446
32.768 kHz | Y101 | SMD2012 | C99009
8.0 MHz | Y102 | SMD5032 | C115962
10u | C421, C422, C423, C424 | C1206 | C13585
10u | C425, C426, C300, C304, C305, C306, C307, C308, C309, C310, C311, C312, C313 | C0805 | C15850
220p | C429 | C0603 | C1603
SS34 | D420 | SMA | C8678
2.2uH | L420 | L1210 | C36828
MWSA0503-10uH | L421 | MWSA0503 | C139506
1 | R420 | R0603 | C22936
68k | R422 | R0603 | C23231
12k | R423, R472 | R0603 | C22790
LMR14020 | U420 | SOP8 | C187824
22u | C450, C451 | C0603 | C59461
Molex MicroSD 47219-2001 | J450 | SDAMB-012
33k | R450, R410, R411, R474 | R0603 | C4216
100u | C410 | TANT-B | C16133
PSM712-LF | D411, D304, D305 | SOT-23 | C32677
ZMM3V3 | D415 | SOD80 | C8056
SMCJ30CA | D418 | SMC | C133648
SMD1206P050TF/24 | F410, F300 | SMD1206 | C209741
AO3400A | Q410, Q411, Q313 | SOT-23 | C20917
4.7k | R412, R302, R303, R307, R308, R313 | R0603 | C23162
6.8k | R413 | R0603 | C23212
3.3n | C471 | C0603 | C1613
330p | C472 | C0603 | C1664
47p | C473 | C0603 | C1671
680p | C474 | C0603 | C1630
470k | R470 | R0603 | C23178
100k | R471, R473 | R0603 | C25803
LMV321IDBVR | U470, U471 | SOT23-5 | C7972
AO3401A | Q300, Q301, Q302, Q303, Q304 | SOT-23 | C306862
0 | R310 | R0603 | C21189
0.1 | R314 | R1206 | C25334
RZ7899 | U300, U303 | SO8 | C92373
ULN2003AD | U301, U304 | SOIC16 | C7512
TC4427 | U302 | SO8 | C20551
10 | R461, R462, R463, R464, R466, R467, R468, R469 | R0603 | C22859
SN74LVC4245APWR | U460 | TSSOP24 | C7859
TJA1021T/20/CM | U440 | SO8 | C128810
PESD1CAN | D430 | SOT-23 | C343993
120 | R430 | R0603 | C22787
TJA1051T/3/1J | U430 | SO8 | C38695
ST/Link 2x5 | P480 | HDR2x5-F-TH-SMD
1u | C600, C607, C609, C610, C611 | C0402 | C52923
100n | C601, C602, C605, C608, C612, C613, C614, C615 | C0402 | C1525
33n | C603 | C0402 | C1585
DNP | C604 | C0402
DNP | C606 | C0402
BTS3028 | Q600 | DPAK | C112639
1k | R600, R601, R616, R617, R622, R626, R627, R628 | R0402 | C11702
68k | R602, R603 | R0402 | C36871
10k | R604, R605, R613, R614, R618, R619, R625 | R0402 | C25744
10 | R606 | R0402 | C25077
22k | R607 | R0402 | C25768
47 | R608 | R0402 | C25118
61.9 | R609 | R0603 | C23092
20k | R610, R611, R612 | R0402 | C25765
100k | R615, R621 | R0402 | C25741
27k | R620, R623 | R0402 | C25771
3.3k | R624 | R0402 | C25890
MCP6004 | U600 | TSSOP14 | C398929
AD8628 | U601 | TSOT23-5 | C29309
STM32F042K6Tx | U602 | LQFP32 | C69216
REF3033 | U603 | SOT-23 | C36658
AP2331TDSA-7 | U103, U480 | SOT-23 | C183303

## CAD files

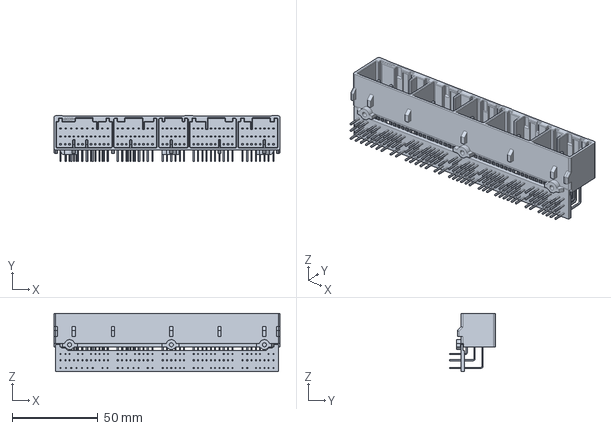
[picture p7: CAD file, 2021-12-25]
8-5353015-1.STEP
131.8 x 26.5 x 34.0 mm

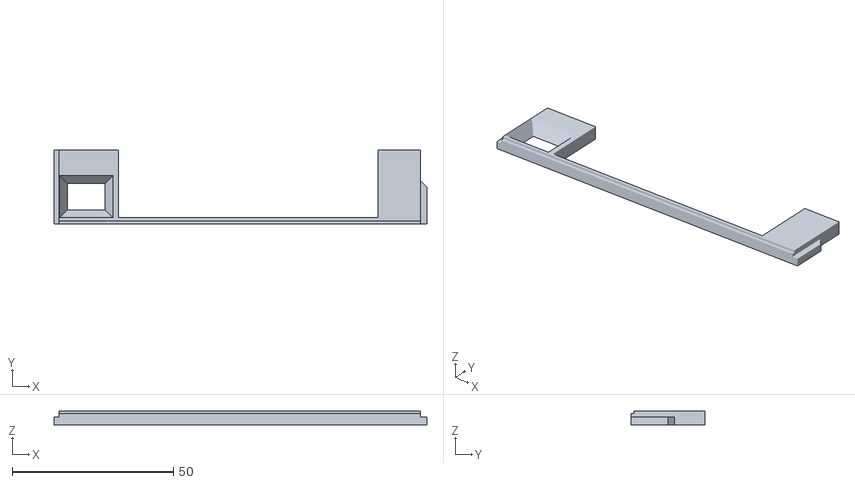
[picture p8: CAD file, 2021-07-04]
hellen72_insert.STL
115.8 x 23.0 x 4.30

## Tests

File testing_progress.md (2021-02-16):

Jan 21, 2020:

- We have blue LED blinking
- We have buzzing if +12v power

Jan 20, 2020:
AndreiKA says https://github.com/rusefi/rusefi/wiki/Hellen72#jumpers

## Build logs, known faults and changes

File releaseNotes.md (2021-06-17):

rev D:
   diode and pull-down VVT, IAC
   SD card by JLC
   silkscreen
   power related fixes - modules 0.2
   2002 vign fix
   second CAN transceiver

rev C: 21 March 2021
   first car driving revision!

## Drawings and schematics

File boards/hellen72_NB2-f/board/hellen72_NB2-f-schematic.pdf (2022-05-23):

# GND GND G

# +5V GND

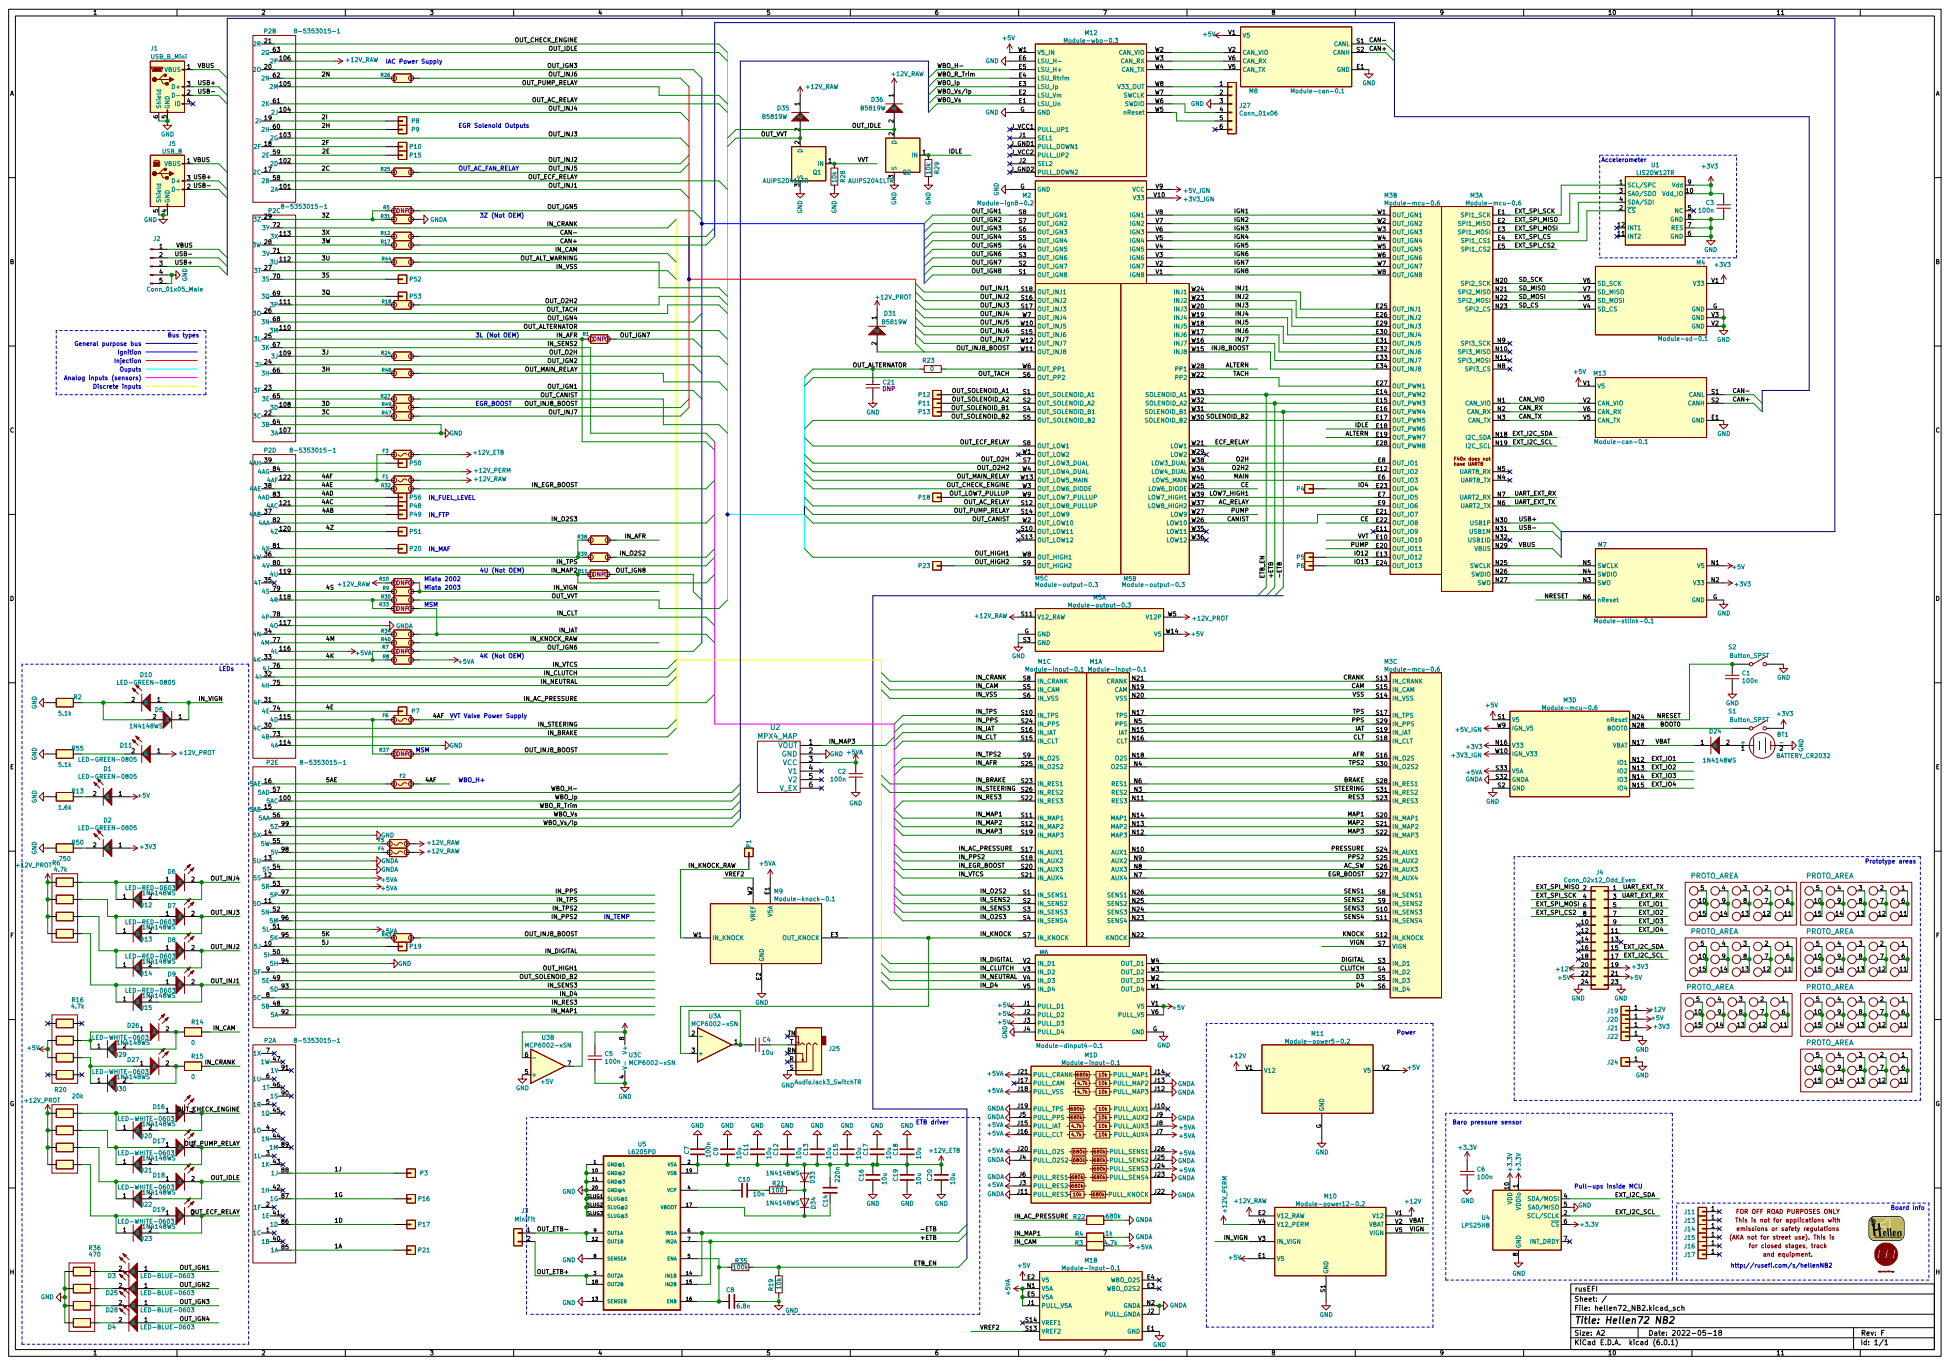
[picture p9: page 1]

IO13 ETB_EN
IAT N15 CLT N16 TPS N17 O2S N18 CAM N19 VSS N20 CRANK N21 KNOCK N22 SENS4 N23 SENS3 N24 SENS2 N25 SENS1 N26 RES2 N3 O2S2 N4 PPS N5 RES1 N6 AUX4 N7 AUX3 N8 AUX2 N9 M1AModule-input-0.1GND G

VVT Valve Power Supply

File: hellen72_NB2.kicad_sch Sheet: / rusEFI GND

Pull-ups inside MCU

for closed stages, track FOR OFF ROAD PURPOSES ONLY
This is not for applications with
emissions or safety regulations
Hellen-One-PCB-logo (AKA not for street use). This is

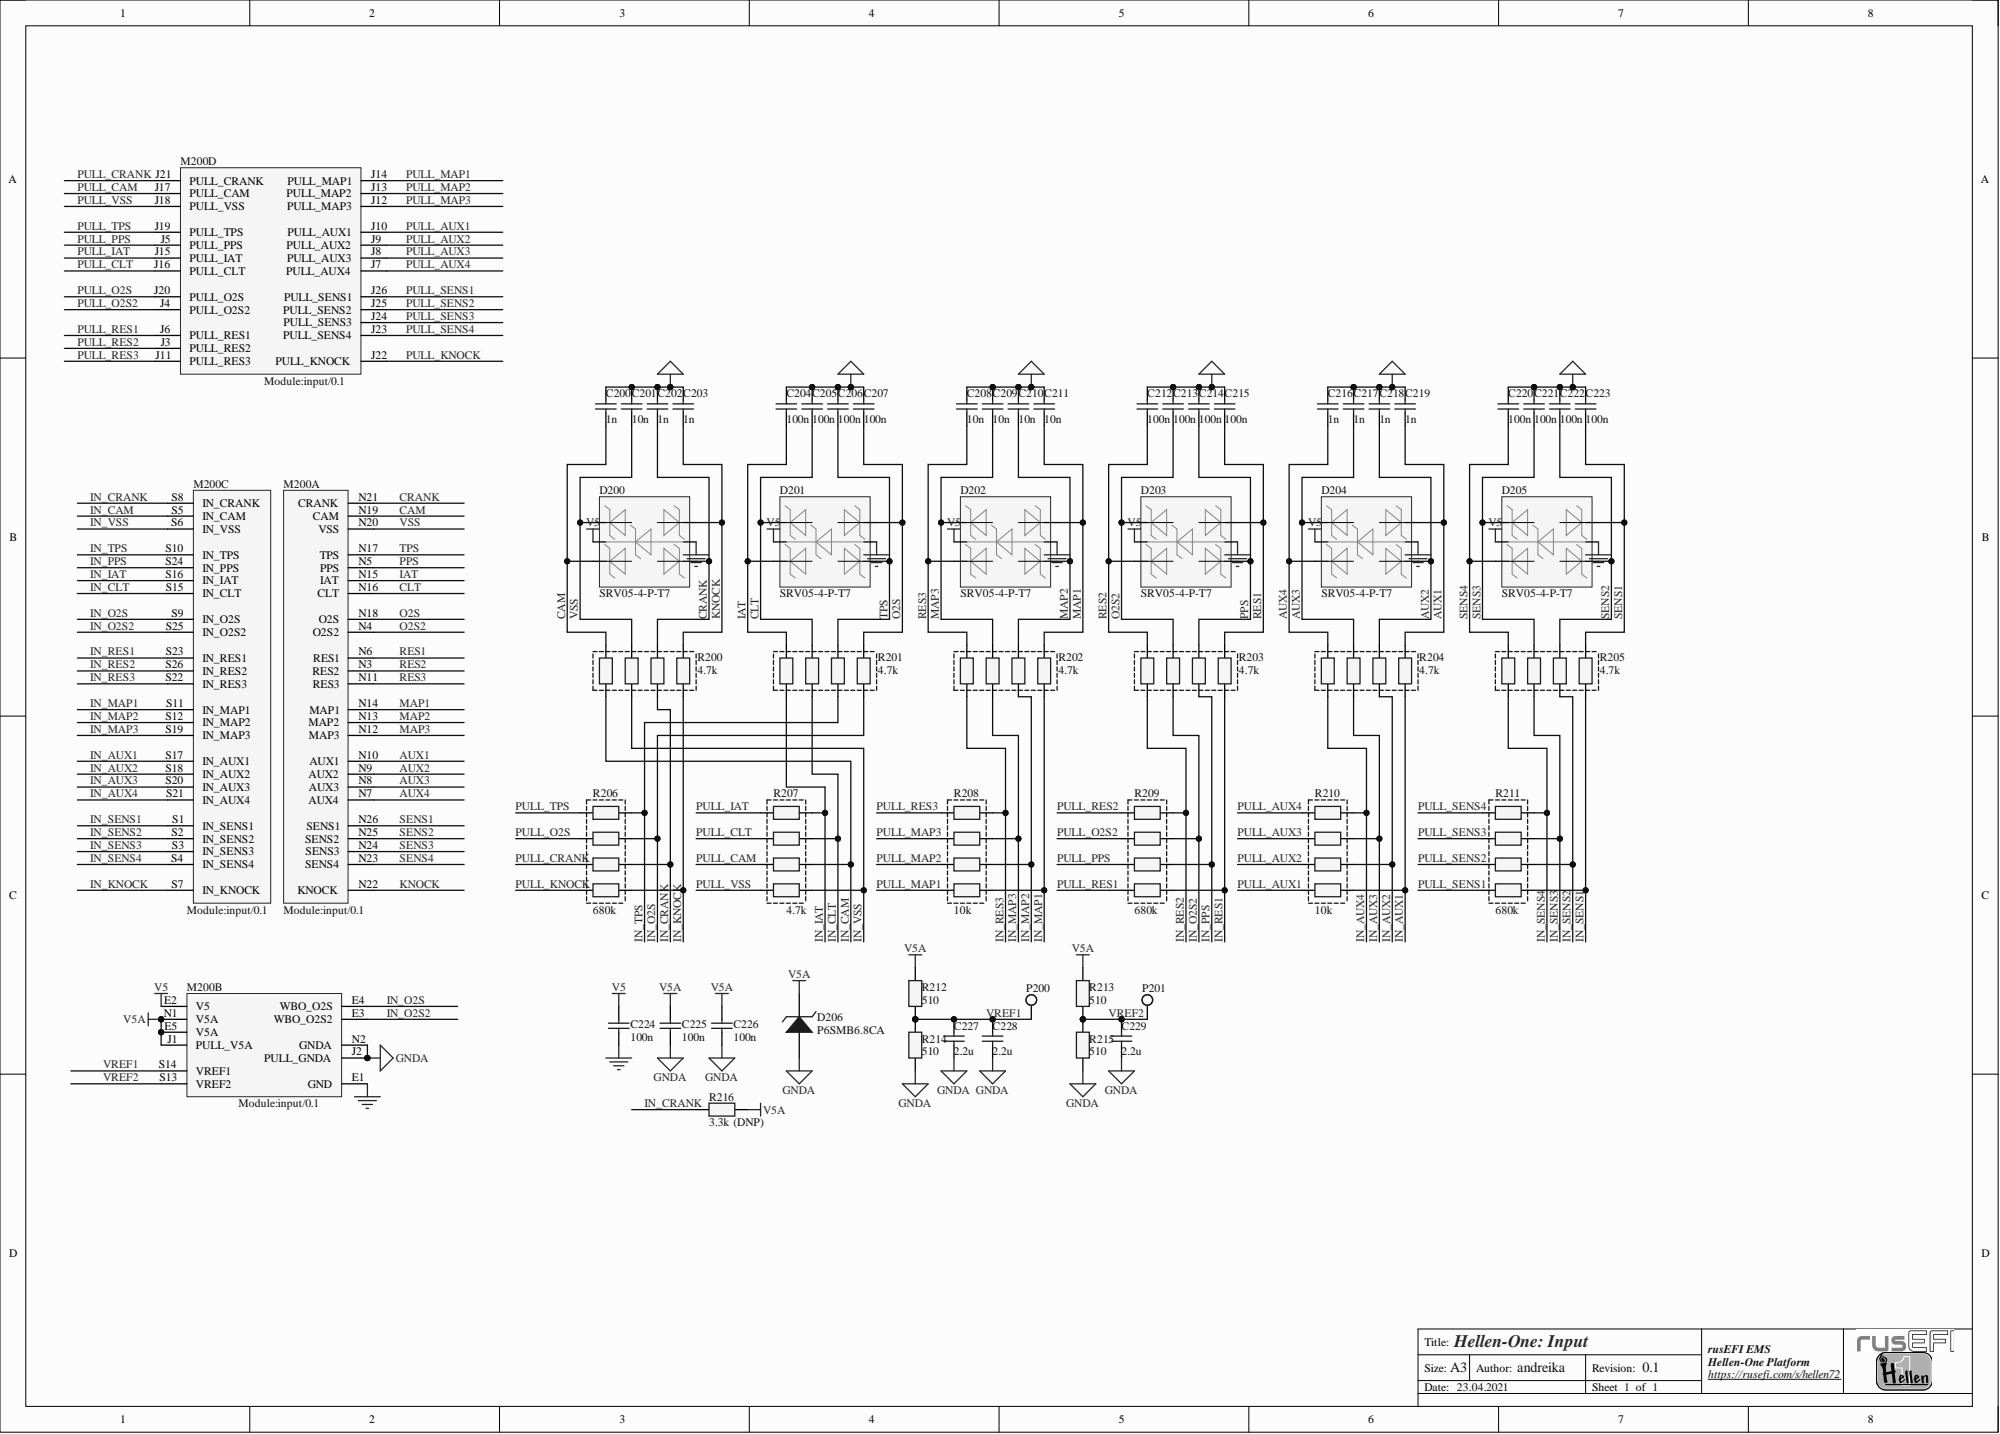
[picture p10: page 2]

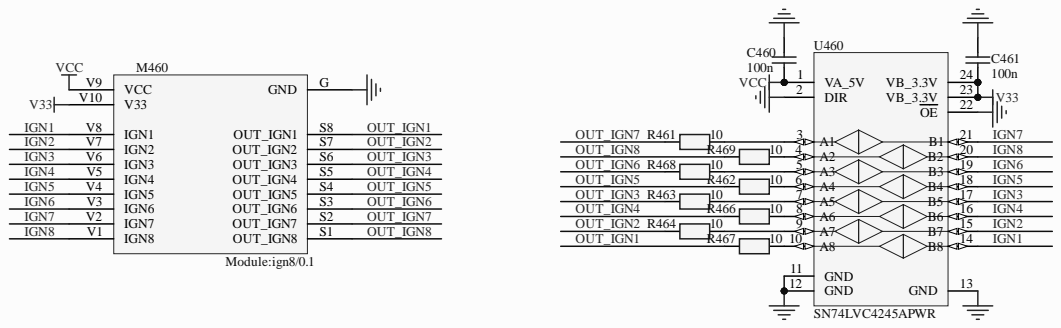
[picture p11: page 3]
tfo rm m/s/h; Size; Dat; Rev; Shee; _IGN; VCC; DIR; LVC4

Hellen-One IGN8 andreika

rusEFI EMS https://rusefi.co
Hellen-One

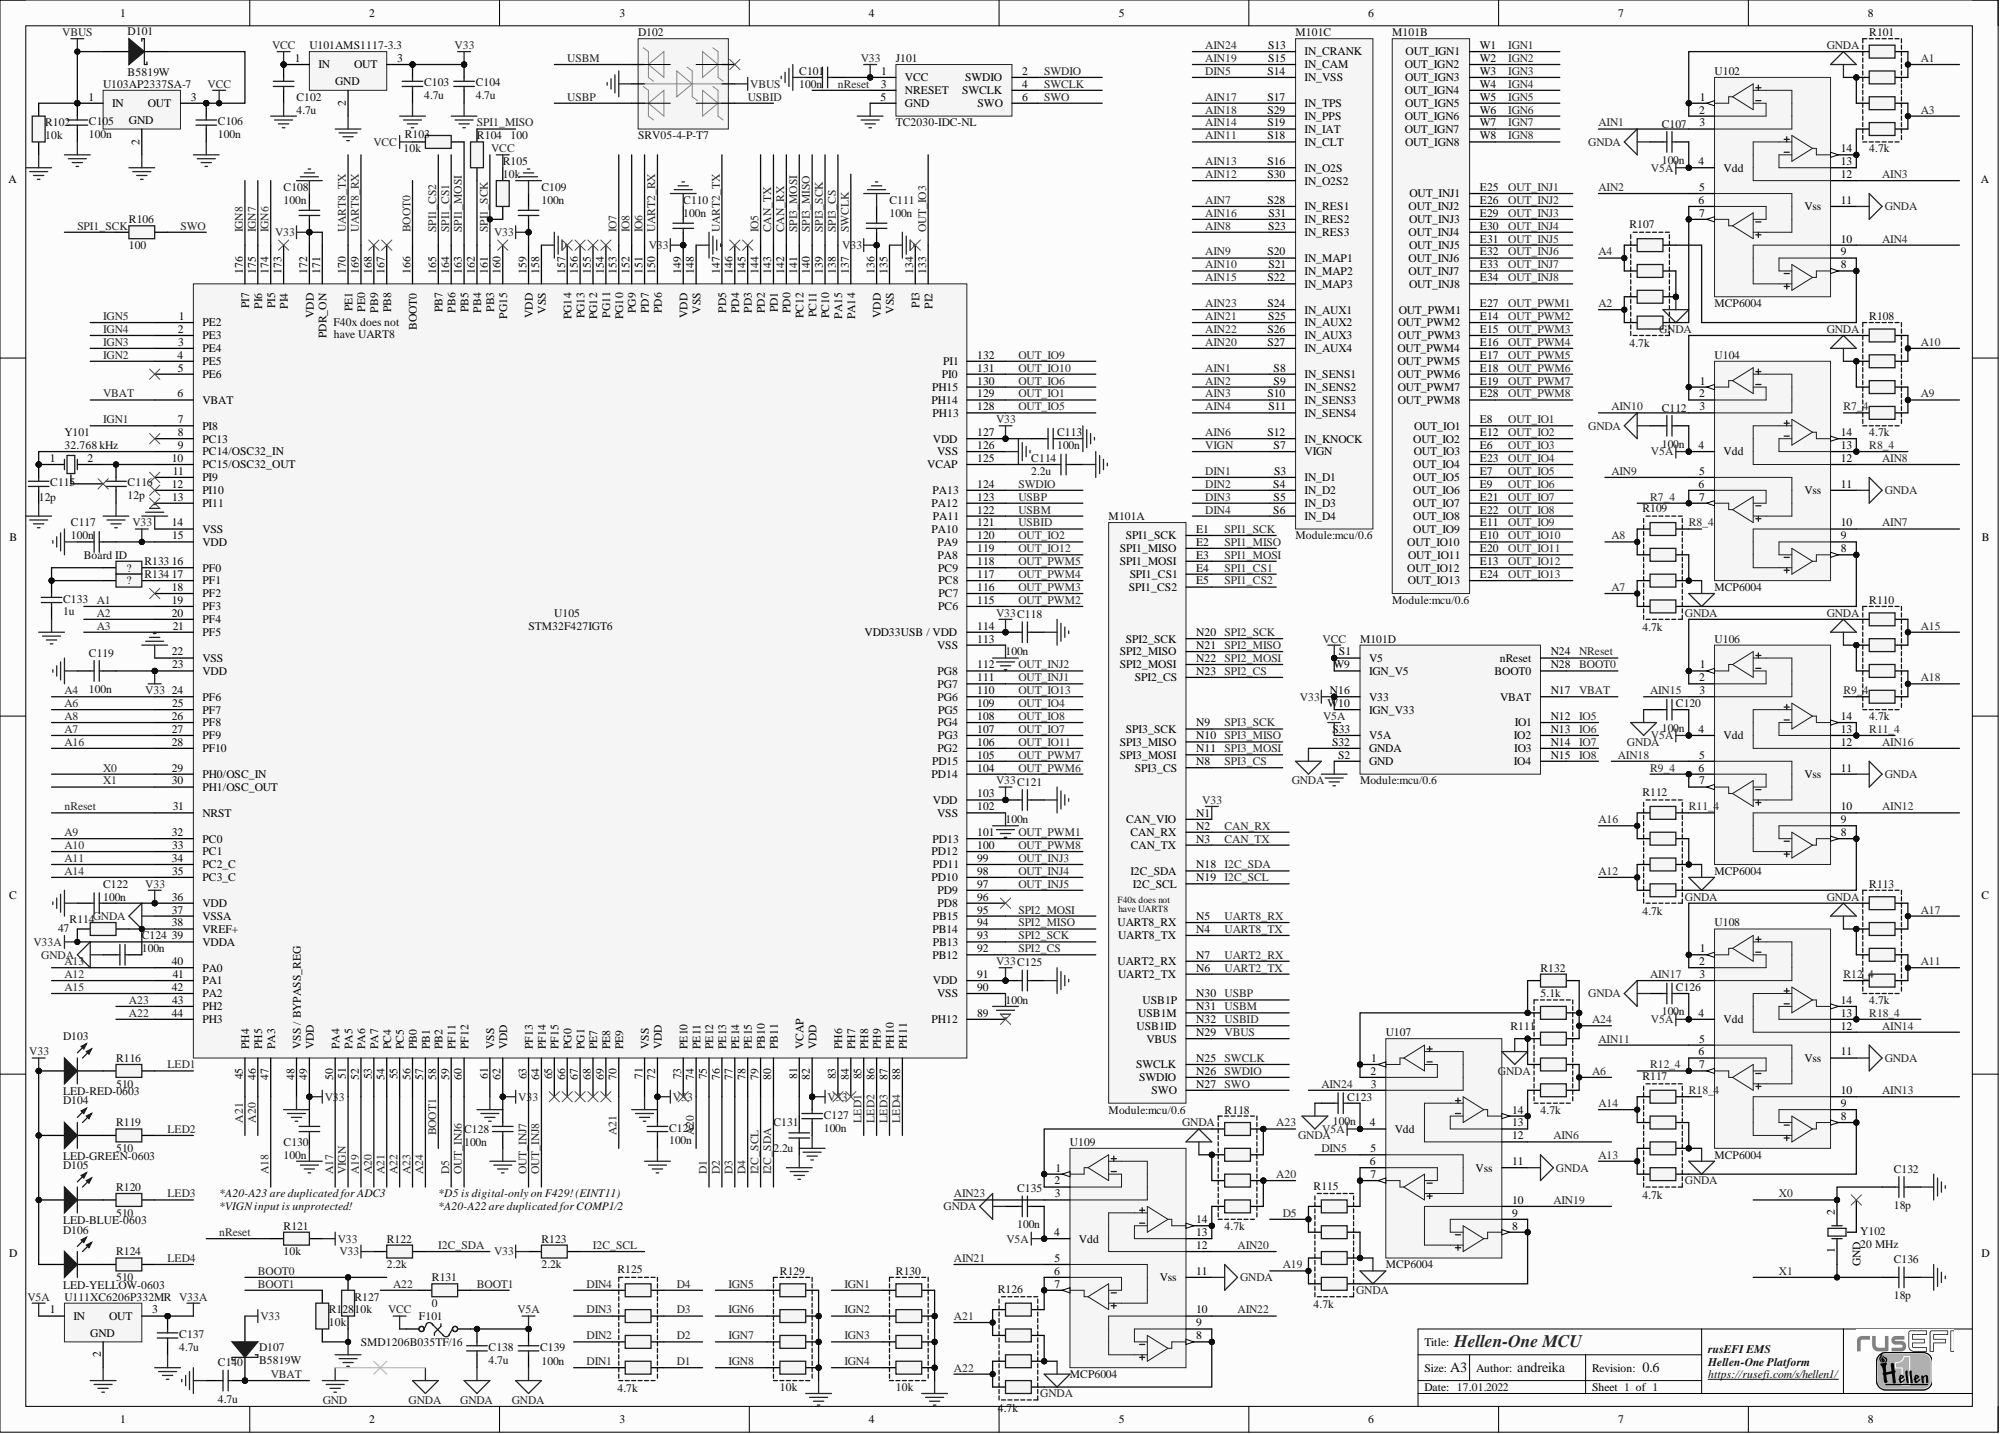
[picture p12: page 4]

D5 *D5 is digital-only on F429!(EINT11)

*A20-A23 are duplicated for ADC3
*VIGN input is unprotected!

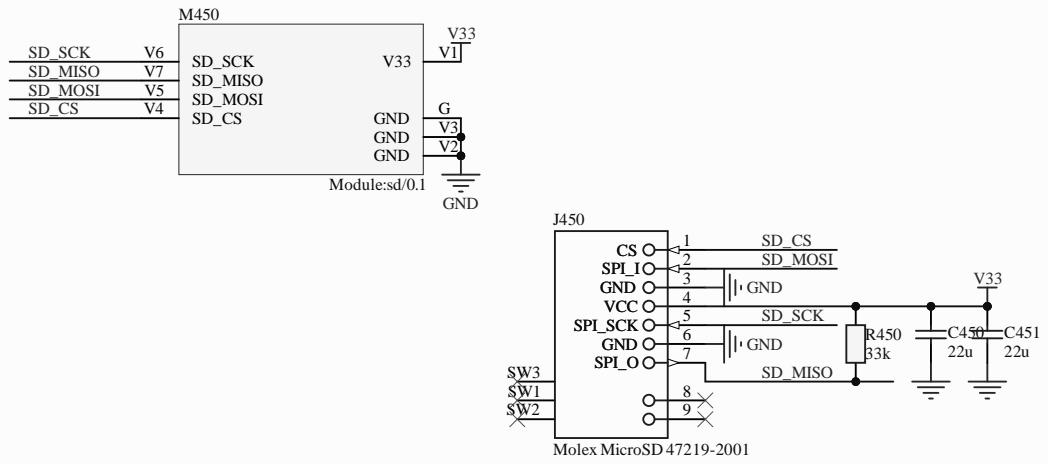
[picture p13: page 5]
2 SPI_I; 3 GND; 4 VCC; 5 SPI_SCK; 6 GND; 7 SPI_O; Molex MicroSD 47219-2001; GND; SD_CS SD_MOSI; SD_SCK; SD_MISO; V2 GND; SD_MOSI V5; SD_SCK V6 SD_MISO V7; Module:sd/0.1; SD_MOSI; SD_SCK SD_MISO

Hellen-One SD-Card

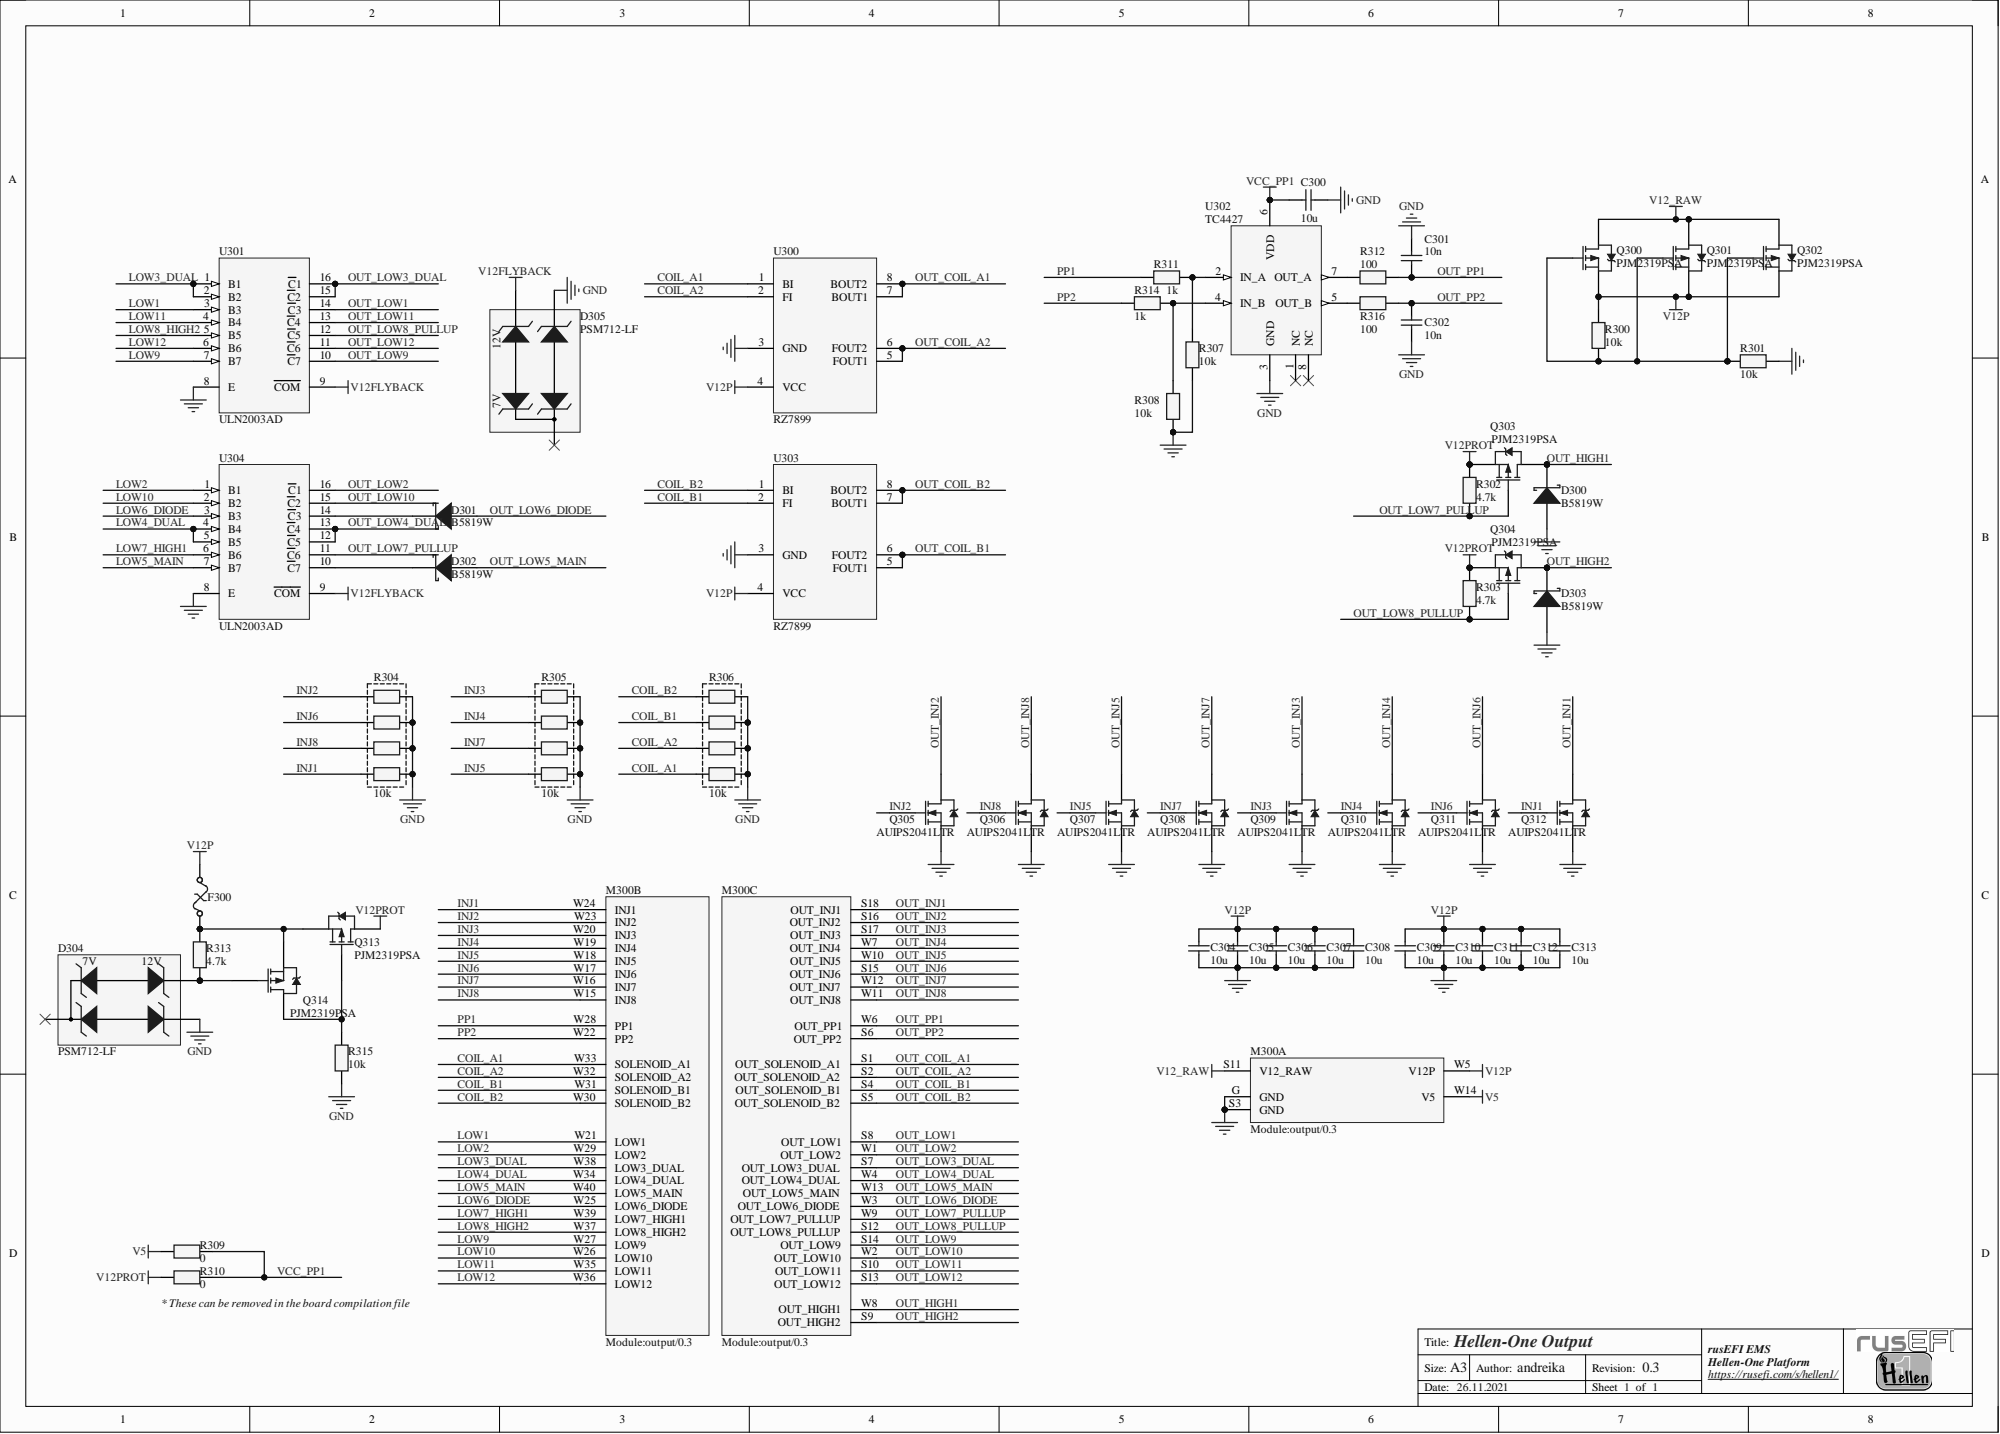
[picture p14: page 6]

* These can be removed in the board compilation file

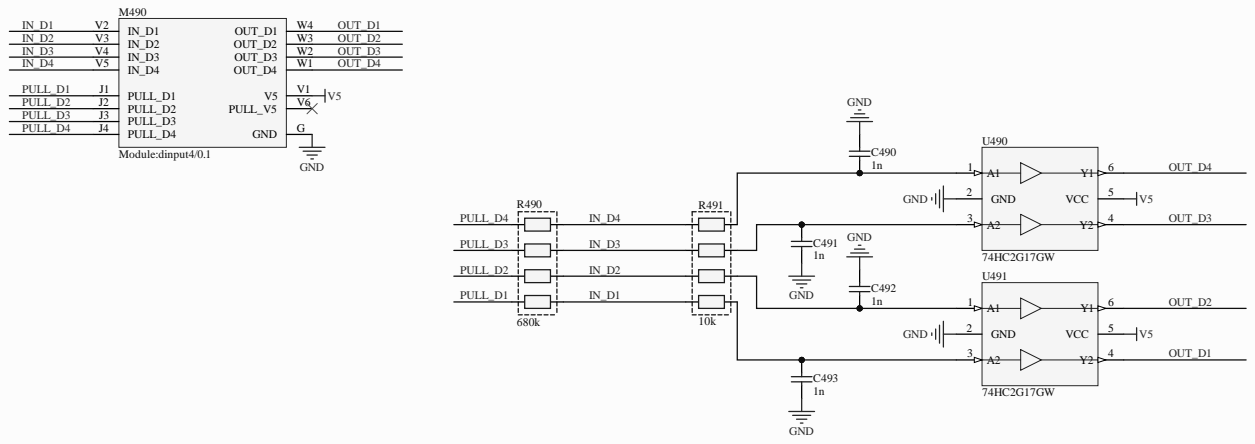
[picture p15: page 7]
tfo rm m/s/h; Size:; Rev; Shee; VCC

Hellen-One VR andreika

rusEFI EMS https://rusefi.co
Hellen-One

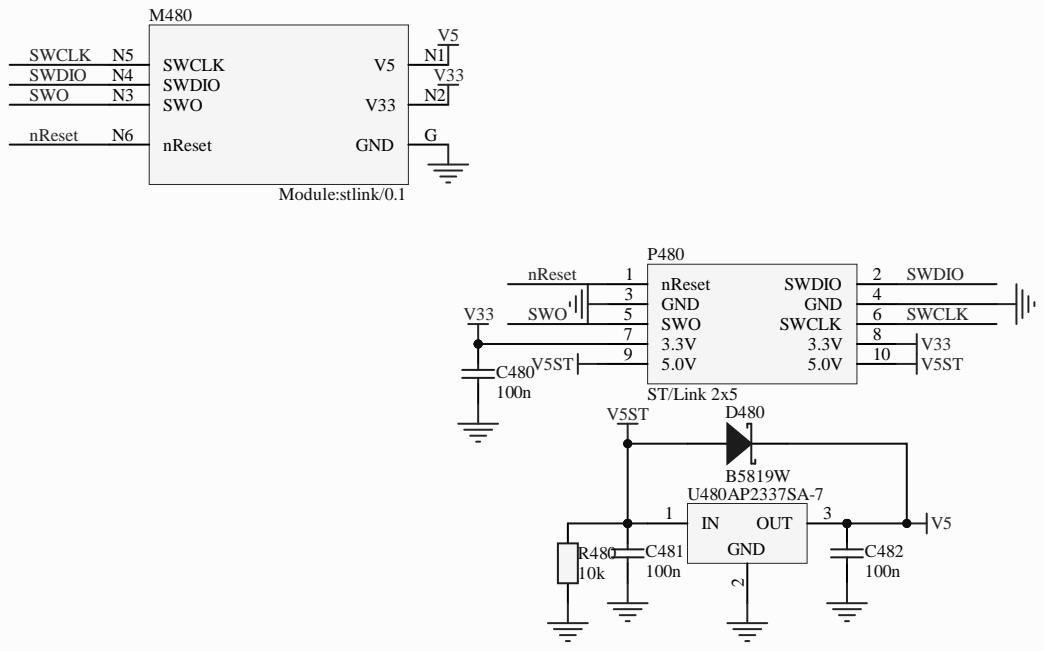
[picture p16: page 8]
nReset 1; SWDIO; GND 3; GND; SWO 5; SWCLK; ST/Link 2x5; nReset; SWO; 2 OUT 3; SWO N3; SWDIO N4; N1 SWCLK N5; nReset N6; Module:stlink/0.1; SWDIO SWO

Hellen-One ST-Link

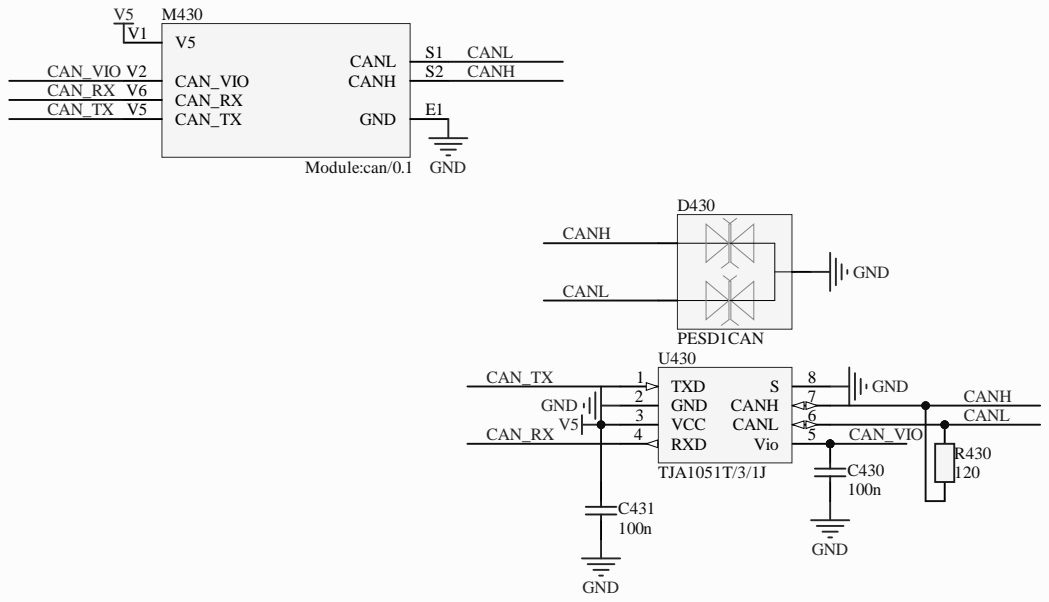
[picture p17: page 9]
PESD1CAN; GND; CANH; CANL; TXD 1 GND 2 VCC 3; Vio; 5 RXD 4; 6 CANH; TJA1051T/3/1J; CANH CANL; CAN_TX; CAN_RX; CAN_VIO; CAN_VIO V2; S2 CANL; CAN_TX V5; CAN_RX V6; Module:can/0.1

Hellen-One CAN

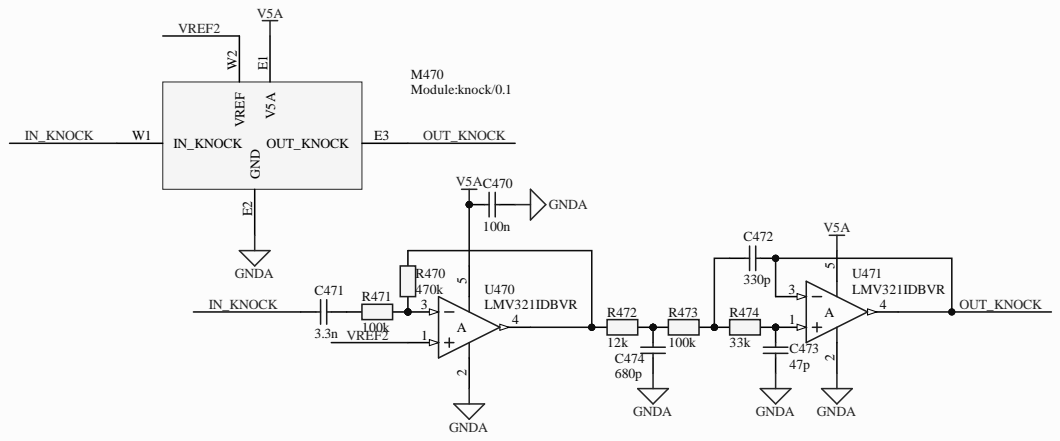
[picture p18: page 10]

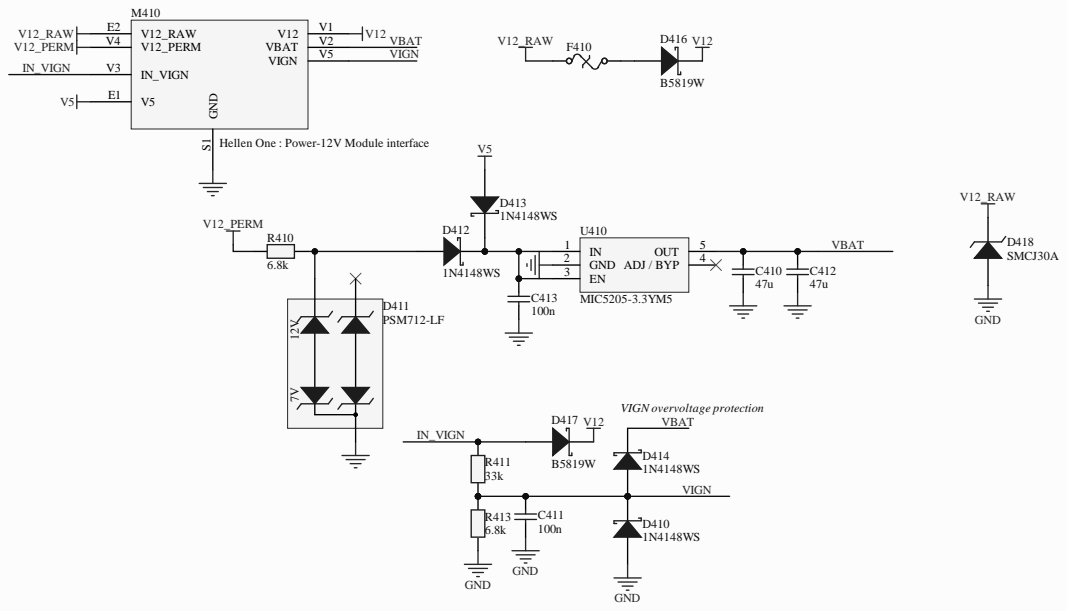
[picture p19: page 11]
tfo rm m/s/h; Hellen-One Power1 2; dreik; Size:; Rev; Shee; VBA; GND S1; Hel; len O; wer-1; terface; VIGN; overvo; tect; 8 SMCJ; 1 PSM7; MIC5

rusEFI EMS https://rusefi.co
Hellen-One

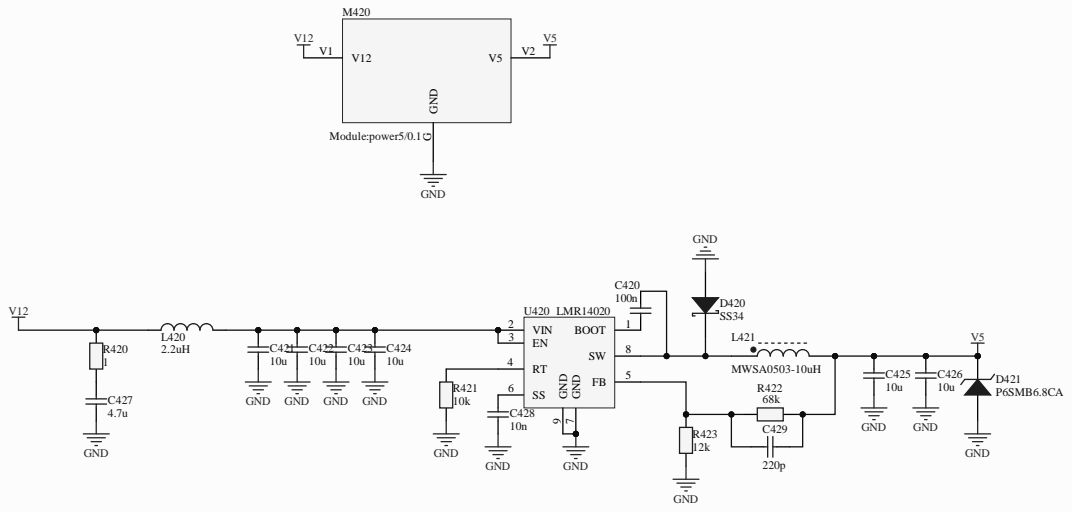
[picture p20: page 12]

1kR600

3.3k R623


Pump Current Sense Nernst Sense

LSU_Vm
Pump Driver Nernst Internal Resistance Measurement

1 VO 2 VI 3 U604 XC6206P332MR GND GND

1 PA4 10 PA5 11 PA6 12 PA7 13 PB0 14 PB1 15 VSS 16 VDDIO2 17 PA8 18 PA9 19 PF0 2 PA10 20 PA11 21 PA12 22 PA13 23 PA14 24 PA15 25 PB3 26 PB4 27 PB5 28 PB6 29 PF1 3 PB7 30 PB8 31 VSSA 32 NRST 4 VDDA

LED-RED-0603 ¹⁰⁰n C⁶⁰⁵ C604 DNP

Nernst Sense Voltage Buffer

1k GND GND R⁶¹⁶ ¹k

File: hellen1-wbo.kicad_sch Sheet: / rusefi.com

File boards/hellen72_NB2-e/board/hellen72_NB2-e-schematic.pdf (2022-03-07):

# P52 R18 P56 P48

# IN_O2S S9 M1C Module-input-0.1 GND


IAT N15 CLT N16 TPS N17 O2S N18 CAM N19 VSS N20 CRANK N21 KNOCK N22 SENS4 N23 SENS3 N24 SENS2 N25 SENS1 N26 RES2 N3 O2S2 N4 PPS N5 RES1 N6 AUX4 N7 AUX3 N8 AUX2 N9 M1AModule-input-0.1

VVT Valve Power Supply WBO_H+

Pull-ups inside MCU

for closed stages, track FOR OFF ROAD PURPOSES ONLY
This is not for applications with
emissions or safety regulations
(AKA not for street use). This is

Hellen-One-PCB-logo


tfo rm m/s/h; Size:; Rev; Shee; VCC; APW

Hellen-One IGN8 andreika

rusEFI EMS https://rusefi.co
Hellen-One


D5 *D5 is digital-only on F429!(EINT11)

*A20-A23 are duplicated for ADC3
*VIGN input is unprotected!

2 SPI_I; 3 GND; 4 VCC; 5 SPI_SCK; 6 GND; 7 SPI_O; Molex MicroSD 47219-2001; GND; SD_CS SD_MOSI; SD_SCK; SD_MISO; V2 GND; SD_MOSI V5; SD_SCK V6 SD_MISO V7; Module:sd/0.1; SD_MOSI; SD_SCK SD_MISO

Hellen-One SD-Card


* These can be removed in the board compilation file

tfo rm m/s/h; Size:; Rev; Shee; VCC

Hellen-One VR andreika

rusEFI EMS https://rusefi.co
Hellen-One

nReset 1; SWDIO; GND 3; GND; SWO 5; SWCLK; ST/Link 2x5; nReset; SWO; 2 OUT 3; SWO N3; SWDIO N4; N1 SWCLK N5; nReset N6; Module:stlink/0.1; SWDIO SWO

Hellen-One ST-Link

PESD1CAN; GND; CANH; CANL; TXD 1 GND 2 VCC 3; Vio; 5 RXD 4; 6 CANH; TJA1051T/3/1J; CANH CANL; CAN_TX; CAN_RX; CAN_VIO; CAN_VIO V2; S2 CANL; CAN_TX V5; CAN_RX V6; Module:can/0.1

Hellen-One CAN


tfo rm m/s/h; Hellen-One Power1 2; dreik; Size:; Rev; Shee; VBA; GND S1; Hel; len O; wer-1; terface; VIGN; overvo; tect; 8 SMCJ; 1 PSM7; MIC5

rusEFI EMS https://rusefi.co
Hellen-One


1kR600

3.3k R623


Pump Current Sense Nernst Sense

LSU_Vm
Pump Driver Nernst Internal Resistance Measurement

1 VO 2 VI 3 U604 XC6206P332MR GND GND

1 PA4 10 PA5 11 PA6 12 PA7 13 PB0 14 PB1 15 VSS 16 VDDIO2 17 PA8 18 PA9 19 PF0 2 PA10 20 PA11 21 PA12 22 PA13 23 PA14 24 PA15 25 PB3 26 PB4 27 PB5 28 PB6 29 PF1 3 PB7 30 PB8 31 VSSA 32 NRST 4 VDDA

LED-RED-0603 ¹⁰⁰n C⁶⁰⁵ C604 DNP

Nernst Sense Voltage Buffer

1k GND GND R⁶¹⁶ ¹k

File: hellen1-wbo.kicad_sch Sheet: / rusefi.com

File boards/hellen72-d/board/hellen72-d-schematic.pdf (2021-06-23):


* AUX2 is used as FUEL_LEVEL
hence the default pullup to +5V

External SD-Card Board

* Rx/Tx reversed for transceiver

tfo rm m/s/h; Hellen72a; dreik; Size:; Rev; Shee; ECF; T_PUMP; ACH; ARN; ERN; IST; CRA; CAM_PU; VSS_PU

rusEFI EMS https://rusefi.co
Hellen-One



D5 *D5 is digital-only on F429!(EINT11)

*A20-A23 are duplicated for ADC3
*VIGN input is unprotected!


2 SPI_I; 3 GND; 4 VCC; 5 SPI_SCK; 6 GND; 7 SPI_O; Molex MicroSD 47219-2001; GND; SD_CS SD_MOSI; SD_SCK; SD_MISO; V2 GND; SD_MOSI V5; SD_SCK V6 SD_MISO V7; Module:sd/0.1; SD_MOSI; SD_SCK SD_MISO

Hellen-One SD-Card

tfo rm m/s/h; Hellen-One Power1 2; dreik; Size:; Rev; Shee; VBA; GND S1; Hel; len O; wer-1; terface; VIGN; overvo; tect; 8 SMCJ; 1 PSM7; MIC5

rusEFI EMS https://rusefi.co
Hellen-One



* These can be removed in the board compilation file

tfo rm m/s/h; Size:; Rev; Shee; VCC; APW

Hellen-One IGN8 andreika

rusEFI EMS https://rusefi.co
Hellen-One

RXD 1 NSLP 2 NWAKE 3; GND; 5 TXD 4; LIN; 6 BAT; 7 INH; TJA1021T/20/CM; UART_TX; UART_RX; UART_RX V2; UART_TX V5; Module:lin/0.1; UART_RX UART_TX

Hellen-One LIN

PESD1CAN; GND; CANH; CANL; TXD 1 GND 2 VCC 3; Vio; 5 RXD 4; 6 CANH; TJA1051T/3/1J; CANH CANL; CAN_TX; CAN_RX; CAN_VIO; CAN_VIO V2; S2 CANL; CAN_TX V5; CAN_RX V6; Module:can/0.1

Hellen-One CAN

nReset 1; SWDIO; GND 3; GND; SWO 5; SWCLK; ST/Link 2x5; nReset; SWO; 2 OUT 3; SWO N3; SWDIO N4; N1 SWCLK N5; nReset N6; Module:stlink/0.1; SWDIO SWO

Hellen-One ST-Link

- 9 U600C MCP6004 | R⁶¹² ²⁰k 100n C⁶⁰⁵ +
10k | R620


Nernst Sense Pump Current Sense Nernst Bias Current Un_sense = 2.7 * (Un - Vm) Virtual Ground Generation Nernst Sense Voltage Buffer

1 PA4 10 PA5 11 PA6 12 PA7 13 PB0 14 PB1 15 VSS 16 VDDIO2 17 PA8 18 PA9 19 PF0 2 PA10 20 PA11 21 PA12 22 PA13 23 PA14 24 PA15 25 PB3 26 PB4 27 PB5 28 PB6 29 PF1 3 PB7 30 PB8 31 VSSA 32 NRST 4 VDDA

1k +3.3V GND GND
LSU_Un Nernst Internal Resistance Measurement

1 VO 2 VI 3 U604 XC6206P332MR GND GND R616 1k R617 1k GND GND

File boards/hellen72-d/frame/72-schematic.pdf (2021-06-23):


* AUX2 is used as FUEL_LEVEL
hence the default pullup to +5V

External SD-Card Board

* Rx/Tx reversed for transceiver


rusEFI EMS https://rusefi.co
Hellen-One

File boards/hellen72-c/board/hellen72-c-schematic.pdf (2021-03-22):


* May be used by WBO module

hence the default pullup to +5V

External SD-Card Board

tfo rm m/s/h; Hellen72a; dreik; Size:; Rev; Shee; ECF; T_PUMP; ACH; ARN; ERN; IST; CRA; CAM_PU; VSS_PU

rusEFI EMS https://rusefi.co
Hellen-One



D5 *D5 is digital-only on F429!(EINT11)

*A20-A23 are duplicated for ADC3
*VIGN input is unprotected!


2 SPI_I; 3 GND; 4 VCC; 5 SPI_SCK; 6 GND; 7 SPI_O; Molex MicroSD 47219-2001; GND; SD_CS SD_MOSI; SD_SCK; SD_MISO; V2 GND; SD_MOSI V5; SD_SCK V6 SD_MISO V7; Module:sd/0.1; SD_MOSI; SD_SCK SD_MISO

Hellen-One SD-Card


Hellen One : Power-12V Module interface



* These can be removed in the board compilation file


RXD 1 NSLP 2 NWAKE 3; GND; 5 TXD 4; LIN; 6 BAT; 7 INH; TJA1021T/20/CM; UART_TX; UART_RX; UART_RX V2; UART_TX V5; Module:lin/0.1; UART_RX UART_TX

Hellen-One LIN

PESD1CAN; GND; CANH; CANL; TXD 1 GND 2 VCC 3; Vio; 5 RXD 4; 6 CANH; TJA1051T/3/1J; CANH CANL; CAN_TX; CAN_RX; CAN_VIO; CAN_VIO V2; S2 CANL; CAN_TX V5; CAN_RX V6; Module:can/0.1

Hellen-One CAN

nReset 1; SWDIO; GND 3; GND; SWO 5; SWCLK; ST/Link 2x5; nReset; SWO; 2 OUT 3; SWO N3; SWDIO N4; N1 SWCLK N5; nReset N6; Module:stlink/0.1; SWDIO SWO

Hellen-One ST-Link

# +5V GND

1u R625


1 PA4 10 PA5 11 PA6 12 PA7 13 PB0 14 PB1 15 VSS 16 VDDIO2 17 PA8 18 PA9 19 PF0 2 PA10 20 PA11 21 PA12 22 PA13 23 PA14 24 PA15 25 PB3 26 PB4 27 PB5 28 PB6 29 PF1 3 PB7 30 PB8 31 VSSA 32 NRST 4 VDDA

Nernst Sense Voltage Buffer

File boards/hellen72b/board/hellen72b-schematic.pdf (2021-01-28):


* May be used by WBO module
GND

* SENS3 is used as FUEL_LEVEL
hence the default pullup to +5V



Hellen One : Input Module interface


D5 *D5 is digital-only on F429!(EINT11)

*A20-A23 are duplicated for ADC3
*VIGN input is unprotected!


2 SPI_I; 3 GND; 4 VCC; 5 SPI_SCK; 6 GND; 7 SPI_O; Molex MicroSD 47219-2001; GND; SD_CS SD_MOSI; SD_SCK; SD_MISO; V33 V1 GND V2; GND V3; SD_CS V4 SD_MOSI V5 SD_SCK V6 SD_MISO V7; GND G; SD_CS SD_MOSI SD_SCK SD_MISO

Hellen One : microSD Module interface

Hellen-One SD-Card


Hellen One : Power-12V Module interface



* These can be removed in the board compilation file

Hellen One : Output Module interface LOW7 W27
LOW12 W29

Hellen One : Output Module interface


RXD 1 NSLP 2 NWAKE 3; GND; 5 TXD 4; LIN; 6 BAT; 7 INH; TJA1021T/20/CM; UART_TX; UART_RX; UART_RX V2; UART_TX V5; GND S1 GND E1; UART_RX UART_TX; LIN V5

Hellen One : LIN Module interface

Hellen-One LIN

PESD1CAN; GND; CANH; CANL; TXD 1 GND 2 VCC 3; Vio; 5 RXD 4; 6 CANH; TJA1051T/3/1J; CANH CANL; CAN_TX; CAN_RX; CAN_VIO; CAN_VIO V2; S2 CANL; S1 CAN_TX V5; CAN_RX V6; GND E1

Hellen One : CAN Module interface

Hellen-One CAN

nReset 1; SWDIO; GND 3; GND; SWO 5; SWCLK; ST/Link 2x5; nReset; SWO; 2 OUT 3; SWO N3; SWDIO N4; V³³ N² V⁵ N¹; SWCLK N5 nReset N6; GND G

Hellen One : ST/Link Module interface

Hellen-One ST-Link

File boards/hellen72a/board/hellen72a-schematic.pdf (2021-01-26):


* May be used by WBO module
GND

* MAP4 may be used as IAT on some configs,
hence the default pullup to +5V



Hellen One : Input Module interface


D5 *D5 is digital-only on F429!(EINT11)

*A20-A23 are duplicated for ADC3
*VIGN input is unprotected!


Hellen One : Power-5V Module interface

2 SPI_I; 3 GND; 4 VCC; 5 SPI_SCK; 6 GND; 7 SPI_O; Molex MicroSD 47219-2001; GND; SD_CS SD_MOSI; SD_SCK; SD_MISO; V33 V1 GND V2; GND V3; SD_CS V4 SD_MOSI V5 SD_SCK V6 SD_MISO V7; GND G; SD_CS SD_MOSI SD_SCK SD_MISO

Hellen One : microSD Module interface

Hellen-One SD-Card


Hellen One : Power-12V Module interface


Hellen One : Knock Pre-amplifier Module interface


* These can be removed in the board compilation file

Hellen One : Output Module interface LOW7 W27
LOW12 W29

Hellen One : Output Module interface


RXD 1 NSLP 2 NWAKE 3; GND; 5 TXD 4; LIN; 6 BAT; 7 INH; TJA1021T/20/CM; UART_TX; UART_RX; UART_RX V2; UART_TX V5; GND S1 GND E1; UART_RX UART_TX; LIN V5

Hellen One : LIN Module interface

Hellen-One LIN

PESD1CAN; GND; CANH; CANL; TXD 1 GND 2 VCC 3; Vio; 5 RXD 4; 6 CANH; TJA1051T/3/1J; CANH CANL; CAN_TX; CAN_RX; CAN_VIO; CAN_VIO V2; S2 CANL; S1 CAN_TX V5; CAN_RX V6; GND E1

Hellen One : CAN Module interface

Hellen-One CAN

nReset 1; SWDIO; GND 3; GND; SWO 5; SWCLK; ST/Link 2x5; nReset; SWO; 2 OUT 3; SWO N3; SWDIO N4; V³³ N² V⁵ N¹; SWCLK N5 nReset N6; GND G

Hellen One : ST/Link Module interface

Hellen-One ST-Link

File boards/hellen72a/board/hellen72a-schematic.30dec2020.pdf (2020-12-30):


* May be used by WBO module
GND

* MAP4 may be used as IAT on some configs,
hence the default pullup to +5V



Hellen One : Input Module interface


Hellen One : MCU Module interface

D5 *D5 is digital-only on F429!(EINT11)

*A20-A23 are duplicated for ADC3
*VIGN input is unprotected!


Hellen One : Power-5V Module interface

2 SPI_I; 3 GND; 4 VCC; 5 SPI_SCK; 6 GND; 7 SPI_O; Molex MicroSD 47219-2001; GND; SD_CS SD_MOSI; SD_SCK; SD_MISO; V33 V1 GND V2; GND V3; SD_CS V4 SD_MOSI V5 SD_SCK V6 SD_MISO V7; GND G; SD_CS SD_MOSI SD_SCK SD_MISO

Hellen One : microSD Module interface

Hellen-One SD-Card


Hellen One : Power-12V Module interface

OUT_KNOCK; VREF2; U470 LMV321IDBVR; IN_KNOCK; IN_KNOCK W1; VREF W²; V5A E2 GND E1

Hellen One : Knock Pre-amplifier Module interface

Hellen-One Knock


* These can be removed in the board compilation file

Hellen One : Output Module interface LOW7 W27
LOW12 W29

Hellen One : Output Module interface


Hellen One : 8-ch Ignition Module interface

RXD 1 NSLP 2 NWAKE 3; GND; 5 TXD 4; LIN; 6 BAT; 7 INH; TJA1021T/20/CM; UART_TX; UART_RX; UART_RX V2; UART_TX V5; GND S1 GND E1; UART_RX UART_TX; LIN V5

Hellen One : LIN Module interface

Hellen-One LIN

PESD1CAN; GND; CANH; CANL; TXD 1 GND 2 VCC 3; Vio; 5 RXD 4; 6 CANH; TJA1051T/3/1J; CANH CANL; CAN_TX; CAN_RX; CAN_VIO; CAN_VIO V2; S2 CANL; S1 CAN_TX V5; CAN_RX V6; GND E1

Hellen One : CAN Module interface

Hellen-One CAN

nReset 1; SWDIO; GND 3; GND; SWO 5; SWCLK; ST/Link 2x5; nReset; SWO; 2 OUT 3; SWO N3; SWDIO N4; V³³ N² V⁵ N¹; SWCLK N5 nReset N6; GND G

Hellen One : ST/Link Module interface

Hellen-One ST-Link


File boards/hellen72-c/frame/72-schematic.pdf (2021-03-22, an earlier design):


* May be used by WBO module

hence the default pullup to +5V

External SD-Card Board


rusEFI EMS https://rusefi.co
Hellen-One

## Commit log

2021-01-01 sent to fab!
    [hellen72a-BOM.20201231.csv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]
2021-01-01 update BOM
    [hellen72a-BOM.csv]
2021-01-14 fresh gerbers
    [72-BOM.csv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]
2021-01-26 update schematics
2021-01-26 original schematics
2021-01-28 Initial hellen72b files
    [72-BOM.csv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]
2021-01-28 Hellen72b kicad6 full source
    [hellen1-72-leds.kicad_sch, hellen1-72.kicad_pcb, hellen1-72.kicad_sch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]
2021-01-28 72b to fab!
    [hellen72b-BOM.01282021.csv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]
2021-02-20 AD files
    [hellen1-72-leds.SchDoc, hellen1-72.PrjPcb, hellen1-72.SchDoc]
2021-02-23 update exported kicad files after refactoring
    [hellen1-72.kicad_sch, hellen1-input.kicad_pcb, hellen1-input.kicad_sch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]
2021-02-23 update AD source files
    [hellen1-72.SchDoc]
2021-03-03 update after refactoring can,lin,sd,stlink
    [hellen1-72.kicad_sch, hellen1-can.kicad_sch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]
2021-03-05 kicad-exported files for vr module
    [hellen1-vr.kicad_pcb, hellen1-vr.kicad_sch]
2021-03-09 dinput4 kicad src
    [hellen1-dinput4.kicad_pcb, hellen1-dinput4.kicad_sch]
2021-03-14 update hellen72c AD source files
    [hellen1-72-leds.SchDoc, hellen1-72.PrjPcb, hellen1-72.SchDoc]
2021-03-14 update hellen72c AD source & frame files
    [72-BOM.csv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]
2021-03-21 first attempt to generate rev.C board files (still problems)
    [hellen72-c-BOM.csv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]
2021-03-21 Update frame & board files: https://github.com/andreika-git/hellen-one/issues/17 https://github.com/andreika-git/hellen-one/issues/16
    [72-BOM.csv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]
2021-03-22 Put USB-mini-vertical + fix https://github.com/andreika-git/hellen-one/issues/18
    [72-BOM.csv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]
2021-03-22 72c fab!
    [hellen72-c-BOM.2021mar22.csv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]
2021-03-23 Move BOM replacements to a separate csv file
    [bom_replace_72-c.csv]
2021-04-10 fix 4k7->4.7k in BOM
    [72-BOM.csv]
2021-04-23 rev.D first attempt + intelligible schematics refactoring https://github.com/andreika-git/hellen-one/issues/31
    [72-BOM.csv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]
2021-05-31 move kicad src files into a separate folder
    [hellen1-72-leds.kicad_sch, hellen1-72.kicad_pcb, hellen1-72.kicad_sch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]
2021-05-31 Hellen72d update (fix #43)
    [72-BOM.csv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]
2021-06-23 update mcu-0.3 kicad-imported source
    [hellen1-mcu.kicad_pcb, hellen1-mcu.kicad_sch]
2021-06-23 rev.D frame
    [72-BOM.csv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]
2021-06-23 rev.D AD source
    [hellen1-72-leds.SchDoc, hellen1-72.PrjPcb, hellen1-72.SchDoc]
2021-06-23 rev.D board & berber files
    [hellen72-d-BOM.csv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]
2021-06-24 rev D
    [hellen72-d-BOM.csv]
2021-09-25 BOM september
    [hellen72-d-BOM.22september2021.csv]
2021-12-17 keep the old files
    [hellen1-72-leds.kicad_sch, hellen1-72.kicad_pcb, hellen1-72.kicad_sch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]
2021-12-17 rev.E schematics draft
    [bom_replace_72_NB1-e.csv, hellen72_NB2.kicad_sch]
2021-12-18 update schem.
    [hellen72_NB2.kicad_sch]
2021-12-25 update schematics with 8-5353015-1
    [8-5353015-1.STEP, hellen72_NB2.kicad_sch]
2022-01-05 update schematics & pcb
    [hellen72_NB2.kicad_sch]
2022-03-07 NB2-rev.E gerbers
    [72_NB2-BOM.csv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]
2022-03-08 JLC parts replacements
    [bom_replace_72_NB2-e.csv, hellen72_NB2-e-BOM.csv]
2022-03-26 iBOM and board image for rev.E
2022-05-23 Auto-generated board
    [72_NB2-BOM.csv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]
